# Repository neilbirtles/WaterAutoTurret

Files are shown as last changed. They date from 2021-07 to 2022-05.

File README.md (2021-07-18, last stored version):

# Water Auto Turret

This is a fully automatic water turret that will track people and fire water at them. Intended to be a toy for children in the summer! Its constructed from a mix of 3D printed parts, aluminium extrusions and various other off the shelf items. The unit is powered by a 12v lead acid battery and plugs into a standard hosepipe push on connector for its water supply. It uses a Khadas VIM3 board to control everything and uses the onboard NPU to do the object tracking.

Full design information will be published here for those that want to make one for themselves

Current stage of development is:
    Mechanics: 90% complete, all functional items are working, just a few covers and minor parts need to be constructed
    Electronics: 95% complete, there are a couple of errors that need to be fixed in the rev2 PCB, but otherwise working
    Software: 50% complete, drivers and test code complete for the water control solenoids and stepper motors and an interface to YOLOv3 is implemented along with initial web front end

## Mechanics

All mechanical items have been designed in Fusion360 - model files to be published. 3D printed items have been printed on a Prusa Mk3S+

## Electronics

Main controller board is a Khadas VIM3. A custom PCB is used to interface to the Water Auto Turret. The PCB mounts a DRV8806 chip for driving 4 solenoids for controlling water flow to the turret, two Trinamic TMC5160 breakout boards for controlling the pitch and yaw stepper motors and some battery monitoring / power control circuitry

## Software 

Interface between the control electronics and the Khadas VIM3 is via WiringPi and SPI dev coded in python so should allow for porting to other SBC such as Raspberry Pi, but there will be obvious limitations for the object tracking if a board without an NPU is used. 

TMC5160_driver.py       - provides a generic TMC5160 driver written in python using WiringPi and SPIdev 
motor_test.py           - exercises the TMC5160 driver and allows both motors to be homed and then manually and automatically moved 

DRV8806_driver.py       - provides a driver for the DRV8806 chip written in python using WiringPi
solenoids_test.py       - exercises the DRV8806 driver and does a simple sequence of closing and opening the 4 valves 

KhadasYolov3Detector    - uses the Khadas Yolo v3 demo from here https://gitlab.com/khadas/aml_npu_app and adds in a simple TCP server to output the detections in JSON format to allow them to be used by the main python application 

Webserver               - initial outline of a flask web front end to provide control info for the water auto turret

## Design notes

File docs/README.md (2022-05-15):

# Water Auto Turret
Welcome to the home of the Water Auto Turret! This project was borne out of the desire to use one of my excellent Khadas VIM3 SBC for something other than crypto currency mining and to provide an excellent (if I do say so myself!) toy for my daughter and her friends during the summer months. The motivation to finish it came from the [1st Khadas Community Competition](https://forum.khadas.com/t/khadas-1st-community-competition/14076) - thank you Khadas! I’ve used the VIM3 to create large crypto mining clusters so I knew they were high performance, well supported and well documented SBCs. One specific feature that I hadn’t used before was the Neural Processing Unit (NPU) and so this project was born to give a real world application to test this feature out. 

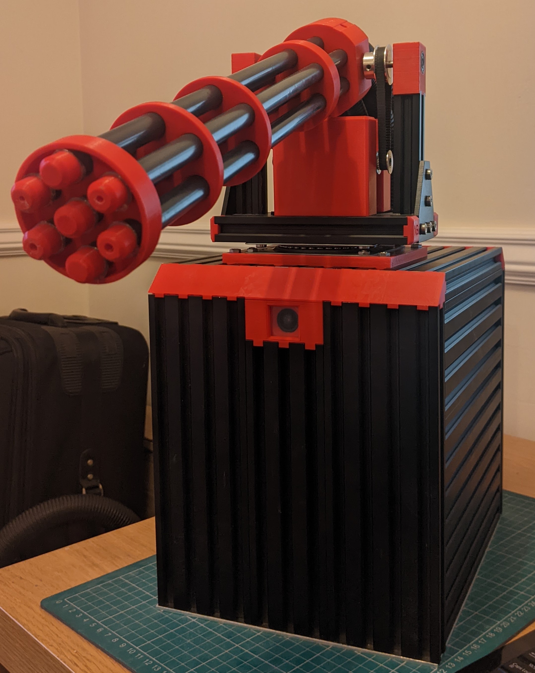
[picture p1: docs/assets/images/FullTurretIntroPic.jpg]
Water Auto Turret Overall Picture


The intention when designing and building this water turret was to minimise the custom design aspects and use off the shelf components (both hardware and software) as far as possible. This didn't always work out as there ended up being lots of custom 3D printed items, a custom PCB, custom extrusions and software however all of these aspects were made significantly easier due to the following companies I sourced parts and software from - I highly recommend them for any similar projects and work!:
* Khadas - OEM of the VIM3, fan, heatsink and the OS08A10 camera used in the project. They also provide excellent support for their products with full 3D CAD models available making the design of 3D printed parts that incorporate them a breeze, great documentation, great supporting software from operating systems to code to access the NPU (including via Python!) and a great forum with lots of community support - [Khadas](https://www.khadas.com/)
* Ooznest - source for all the aluminum extrusions, brackets and motors used in this project. Their fast, excellent and very accurate cut to size and tapping service for the extrusions made the core mechanical aspects of this project really easy to put together - [Ooznest](https://ooznest.co.uk/) 
* Prusa - source for my Prusa i3 MK3S+ 3D printer and the Prusament filament used to 3D print all parts in this project. The accuracy from this printer allowed repeatable production of friction fit parts making assembly of the Water Auto Turret significantly easier - [Prusa](https://www.prusa3d.com/) 
* Accu - source for all the fixings used in this project - this might not sound like the most exciting aspect but being able to easily and quickly (next day) get fixings of the lengths needed in stainless steel without massive minimum order quantities allowed rapid progress to be made without adding additional constraints / time into the design process. My order history on their site attests to their usefulness as ive bought everything from M1.4 screws to the M12 coach bolts used in making my daughters monkey bars (can be seen in the background of the demo video!) - [Accu](https://www.accu.co.uk/)

Heres a short video of the Water Auto Turret in action during its testing phase

<iframe width="560" height="315" src="https://www.youtube.com/embed/ZMWd3soy9fM" title="YouTube video player" frameborder="0" allow="accelerometer; autoplay; clipboard-write; encrypted-media; gyroscope; picture-in-picture" allowfullscreen></iframe>

The Water Auto Turret has been built from black anodised extrusions, Lipstick Red Prusament PLA for all 3D printed parts and stainless steel fixings because I like the combination of these colours but this is obviously left up to the individual to pick the colour scheme and combinations. The block diagram for the Water Auto Turret can be found below.

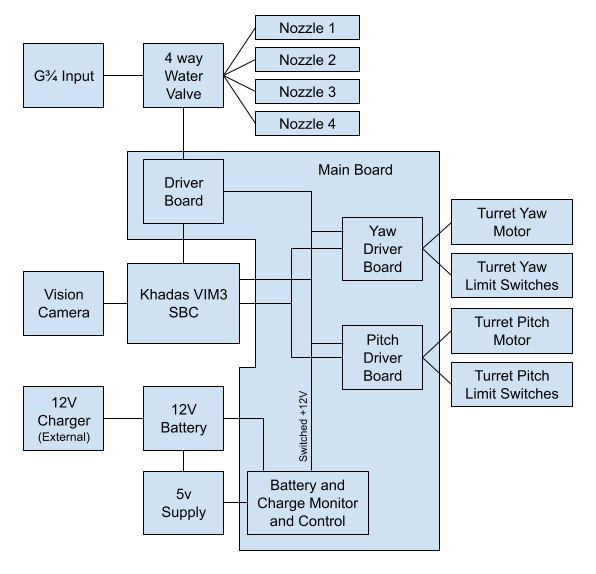
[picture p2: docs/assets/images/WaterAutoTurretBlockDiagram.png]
Block Diagram of the Water Auto Turret


### Controller
The heart of the system is the Khadas VIM3 SBC it provides the overall controller interfacing to a camera to provide the vision inputs, running the software for target identification and tracking (see the Software Description) and interfacing to a custom Main Board that provides:
* Control for pitch and yaw motors
* Control for water flow via solenoid valves 
* Power control with battery charging identification and voltage monitoring

The camera used in the system is a Khadas OS08A10 8MP HDR Camera. This plugs into the VIM3 via the MIPI-CSI port. The camera is housed in a custom 3D printed enclosure {02 Camera Enclosure} (the design of which was made way easier by the use of the Khadas provided CAD model of the camera!) that joins onto the main electronics enclosure that houses the VIM3 and Main Board.

### Main Board

The Main Board (see the [Controller PCB](https://github.com/neilbirtles/WaterAutoTurret/tree/main/Controller%20PCB)) for circuit diagrams, PCB layouts and firmware for the embedded microcontroller) for the system is designed as a daughter board for the VIM3 that plugs on via the 40 pin GPIO header and has fixing holes aligned to the VIM3 ones allowing both boards to be screwed together into the custom 3D printed electronics enclosure. Between the Main Board and VIM3 is a 3D printed heatsink cover to help direct airflow and a set of 3D printed spacers to keep the two boards correctly spaced when screwed in. A securing slot is also provided for the VIM3 wifi antenna to hold it in place in the enclosure. The {[00 Electronics Enclosure Base](https://github.com/neilbirtles/WaterAutoTurret/blob/main/3D%20Printable%20Parts/Electronics%20Enclosure/00%20Electronics%20Enclosure%20Base%20(Supports%20Needed).stl)} and {[01 Electronics Enclosure Lid](https://github.com/neilbirtles/WaterAutoTurret/blob/main/3D%20Printable%20Parts/Electronics%20Enclosure/01%20Electronics%20Enclosure%20Lid.stl)} have been designed to minimise the chances of water ingress whilst at the same time allowing all the required connections and airflow. All connections are via the bottom on the enclosure and are via grommets to minimise open areas. Air flow is via the front face of the enclosure with a plenum chamber (with water drain holes) to prevent direct water access. The air from this chamber is directed into the side of the VIM3 heatsink where it is pulled across the heatsink via the VIM3 heatsink fan. Exhaust air is pulled out of the enclosure via a fan in the bottom. A grommet strip is used to provide a seal between the lid and base and the interface to the camera housing has a lip preventing water entering via this direction as well. 

The Main Board provides control of the pitch and yaw motors for the Water Auto Turret Barrel through the use of TMC5160 motion controllers. These simplify overall system and software design by just allowing target positions to be sent to the controllers (post calibration) with the TMC5160 taking care of the complicated motor and position control. To further simplify the design [TMC5160 Breakout Boards](https://www.trinamic.com/support/eval-kits/details/tmc5160-bob/) have been used that incorporate the motor drive MOSFETs and all passives needed on a small form factor PCB that simply plugs into the Main Board via pin headers. These boards interface to the VIM3 via the SPI interface (GPIO pins 16 => CLK, 35 => SDO, 37 => SDI), with VIM3 GPIO pins used as chip select (CS) lines (GPIO pins 22 => Yaw Motor CS, 23 => Pitch Motor CS). The TMC5160 motion controller boards also incorporate lines for the use of limit switches. Two are used for each of the pitch and yaw motors to allow for homing. The motion controllers are capable of switch free homing but requires the motors to be running at reasonable speeds and to hit physical limits for sensing neither of which are present in this system.

### Water Control

Control of the water flow is provided via a standard 4 way normally closed solenoid valve. This valve has a standard G3/4 threaded input and 4 10mm outlets, each of which is individually controlled via a 12v solenoid. These solenoids are in turn controlled via a DRV8806 mounted on the Main Board that provides the required drivers for the solenoids and interfaces to the VIM3 via a simple clock and latch serial interface (GPIO pins 29 => SDI, 31 => SCLK, 32 => Latch, 33 => Reset (not used but wired in case useful). 4 of the 6 barrels on the overall Water Auto Turret barrel can therefore be used to squirt water at targets. Different size nozzles have been provided as 3D printed parts to allow for different ranges and volumes of water. These nozzle sizes can be configured for the water pressure present and the desired ranges. The number of nozzles used simultaneously can also affect the distance depending on the available water pressure. These nozzles are designed to slot inside the individual barrels and have been hot glued in place which provides a good balance between being able to change and a decent water seal. The solenoid valve has been chosen to be able to cope with mains water pressure and in the system I use has a standard push fit hosepipe fitting screwed onto the G3/4 thread to allow easy connection and disconnection from the water supply.

### Power

The entire system is powered via a 12v sealed lead acid battery. This provides a water safe way of providing the power required in a portable manner. No charging control circuit is contained in the system but a connector is provided to enable a standard 12v sealed lead acid battery charger to be connected to the system. A fan is provided (in a 3D printed housing to prevent water damage) to ensure ventilation of the Water Auto Turret base when the battery is charging. The Main Board monitors for this charging power input and also monitors the battery voltage to ensure that the battery is not over discharged. If either of these conditions are detected then the power to the VIM3, motor and solenoid controllers is removed and only restored once both these conditions are removed. This is achieved via a latching 12v relay to reduce power consumption. These control aspects are provided via a small PIC microcontroller that also provides indication (via LED on the power and water inlet 3D printed part) if either of these conditions are encountered. The firmware for this microcontroller can be found in the firmware subfolder of the PCB folder. The C source code is fully commented and is fairly simple so no explanation is provided here.

### Project Status

The Water Auto Turret is currently fully functional and capable of identifying, tracking and shooting targets (i.e. children!) with water. In work is an improvement to the frame rate of the tracking algorithm and improvement to accuracy of water shooting - especially in the more extreme left and right arcs of fire. 

### Build Guide

A complete description, build guide and bill of materials can be found in this repository so should be relatively straightforward for anyone that wants to replicate the project. Any questions then please just ask - I am more than willing to help.

Build Guide and Descriptions:
* [VIM3 Setup](VIM3Setup.md)
* [Software Description](SoftwareDescription.md)
* [3D Printed Parts](3DPrintedParts.md)
* [Mechanical Assembly](MechanicalAssembly.md)
* [Electronics Assembly](ElectronicsAssembly.md)
* [Full Bill of Maerials and Equipment Breakdown Strucutre](https://github.com/neilbirtles/WaterAutoTurret/tree/main/BoMandEBS.xlsx)

### 3D Models

A complete interactive 3D Model for the Water Auto Turret can be found [here](https://a360.co/3vnJYny) and an export of all the 3D components in both Fusion360 and step file formats can be found here [3D Models](https://github.com/neilbirtles/WaterAutoTurret/tree/main/Fusion360%20Files)

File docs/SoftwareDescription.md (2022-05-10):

# Software Description
The software for the Water Auto Turret has been implemented in four main parts:
* A Web Application using the Flask framework to provide the user interface
* The Khadas Software Neural Network (Python API) to carry out the computer vision to identify potential targets
* A turret controller that takes the potential targets and converts this to turret movement information and feeds this information back to the web front end
* Low level drivers to control the motors, solenoids etc.

The code has been pretty thoroughly commented so should be relatively self explanatory however and overview is given below. I am not a software developer and have self taught myself python so welcome any feedback on improvements and or better ways of implementing this code!

### Web Application
This is a standard Flask web application that is started using the command `python3 autoturret.py`

Within the [\_\_init__.py](https://github.com/neilbirtles/WaterAutoTurret/blob/main/Auto%20Turret%20Control%20Software/autoturretwebapp/__init__.py) file the following are initialised:
* motors - provides setup of the SPI / GPIO interfaces, initialisation (inc chip select pin definition) and carries out the homing for the  pitch_motor and yaw_motors. Both motors use the lower level TMC5160_driver for interfacing to the TMC5160 Breakout Boards.
* solenoids - provides setup and initialisation of the solenoid interface including the GPIO pins used for the interface to the lower level DRV8806 driver.
* detection_model_params - provides and initial setup of parameters for the detection model. Created to provide easier change in the future
* turret_controller - the turret controller which is where all the neural network processing is carried out. This is spawned in a separate thread to prevent the web app becoming blocked. Outputs from this thread are loaded into a standard Python Queue to allow the outputs to be grabbed by the web app to display on the front end.
* app_thread_pool - provides the thread pool (that the turret_controller is spawned in), events for notifications into/out of the thread and also the pipeline for exchanging information out of the thread

After this initialisation the Flask app is started and the system is ready for targets!

In the routes.py file the generate() function attempts to grabs video frames from the Queue and allows them to be displayed on the web front end. The rate this grab happens is adjusted to slightly faster than the current frame rate to get a decent refresh rate on the screen without this function looping instantly and using all processing power (as it did when I first wrote it…)

### KSNN Yolov3
The Water Auto Turret uses the Yolo v3 model to carry out the object detection and tracking. The code for this can be found in the [turret_controller.py](https://github.com/neilbirtles/WaterAutoTurret/blob/main/Auto%20Turret%20Control%20Software/autoturretwebapp/turret_controller.py) file and draws on the Khadas examples. The Yolo v3 model and lib files are the standard Khadas provided ones. 

The detection works as follows:
* Setup the KSNN
* Initialise the neural network with the Yolo v3 model
* Setup the opencv capture devices
* Loop around the following:
  * Grab a video frame
  * Carry out inference
  * Transform the returned data into the format required for post processing
  * Extract the bounding boxes, associated class names and probability scores from the returned data
  * Scale the grabbed frame to be the right size to display in the web front end
  * Get targets from the neural network returned data (including marking these up in the grabbed frame
  * Pass the grabbed frame into Queue to allow it to be grabbed by the web front end for display

### Turret Controller
The turret control software can also be found in the [turret_controller.py](https://github.com/neilbirtles/WaterAutoTurret/blob/main/Auto%20Turret%20Control%20Software/autoturretwebapp/turret_controller.py) file. The target detection loop through all the object detections passed out from the neural network processing and does the following checks on each to identify targets:
* Checks if the detected object is a “person” and if the probability is above the detection threshold
* If both are true then annotate the target in the image frame with “TARGET ACQUIRED”
* Calculate the mid point of the target to allow the Water Auto Turret to target it with water
* Draw a red * at the midpoint of the target in the image frame
* Scale the target image coordinates into the pitch and yaw step ranges (calculated during the initial homing procedure)
* Check if the difference in the new target coordinate is greater than the move threshold in both pitch and yaw motions
* If the difference is greater than the move threshold then move the appropriate motor(s) to the new target positions
* If there are one or more targets then turn on the water and if there arent then turn off the water (at the current time all 4 water ports are turned on or off at the same time)

### Low Level Drivers
#### TMC5160
The driver for this is provided in [TMC5160_driver.py](https://github.com/neilbirtles/WaterAutoTurret/blob/main/Auto%20Turret%20Control%20Software/autoturretwebapp/TMC5160_driver.py). The driver exposes all the functions of the TMC5160 that are currently used and have been used in development but does not provide all features of the TMC5160 device. The internal __read_from_TMC_5160 and __write_to_TMC5160 functions provide the interface direct to the chip. Other higher level functions are exposed from the driver such as “home”. The code in this file is well documented and is directly derived from the [TMC5160 datasheet](https://www.trinamic.com/fileadmin/assets/Products/ICs_Documents/TMC5160A_datasheet_rev1.16.pdf) so should be read in conjunction with the datasheet to get a full understanding of how it works.

#### DRV8806
The driver for this is provided in the [DRV8806_driver.py](https://github.com/neilbirtles/WaterAutoTurret/blob/main/Auto%20Turret%20Control%20Software/autoturretwebapp/DRV8806_driver.py). This should again be read in conjunction with the datasheet for the [DRV8806](https://www.ti.com/lit/gpn/drv8806) but this is much simpler than the TMC5160 as the interface is essentially - set or reset the data bit to indicate a solenoid driving being on or off respectively, clock this data bit into the device by strobing the clock line, repeat this 3 times more to get data bits for all 4 outputs into the device and then latch that data into the outputs. Again the code is documented so should be easy to understand. 

### Tests
In the “Tests” folder there are some standalone test files that can be used when debugging the system or for testing during assembly
* [motor_test.py](https://github.com/neilbirtles/WaterAutoTurret/blob/main/Auto%20Turret%20Control%20Software/Tests/motor_test.py) - allows for manual homing and setup whilst providing low level feedback from the driver code. The functionality for this can be seen from the code or from running the file and reading the prompts
* [solenoids_test.py](https://github.com/neilbirtles/WaterAutoTurret/blob/main/Auto%20Turret%20Control%20Software/Tests/solenoids_test.py) - provides a sequence that turns on each solenoid valve in sequence 0.5 seconds apart, waits 1 second and then turns them off in sequence 0.5 seconds apart. This produces an audible clicking that can be used to ensure all solenoids are working

## Future Software Development
The Water Auto Turret is currently fully functional, however its always possible to get better! For this reason the following areas of software are currently under development:
* Improved target tracking using OpenCV for detection at a reduced frame rate and then using the much lighter weight [Dlib for tracking](http://dlib.net/correlation_tracker.py.html) with the aim or providing more frequent updates to the targeting 
* Improved alignment between objects being tracked and targeting - at the moment this is a linear scale relationship and this doesn't work as well as it could as the target moves away from centre

[{Home}](README.md) [{Next}](3DPrintedParts.md)

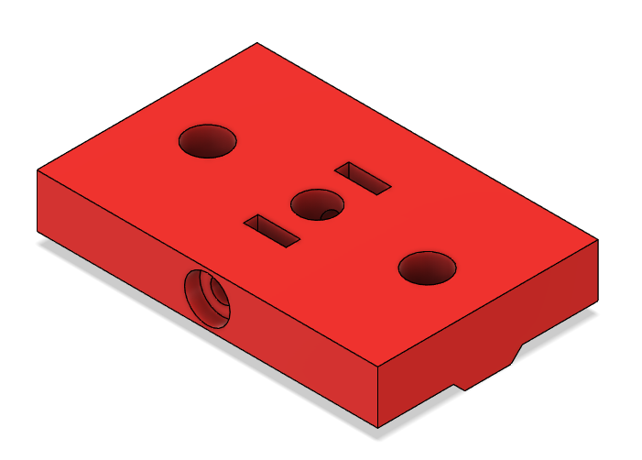
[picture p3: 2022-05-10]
docs/assets/images/BarrelMountRotaryAttachment.PNG

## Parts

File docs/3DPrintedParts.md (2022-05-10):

# 3D Printed Parts

All 3D printed parts were printed from PLA on a Prusa Mk3s, using standard settings. Only those parts that have their names appended with “(Supports Needed)” need supports enabled, all other parts have been designed specifically to be printed support free. All parts have been saved in the correct orientation for printing to simplify the process. As they can be added to your slicer of choice, sliced and printed. The variable layer height feature was used on all the parts to speed up the print time as there are quite a lot of parts to be printed!

On a well setup printer the parts will be of the correct size to fit together, with many of the parts being friction fit into the aluminum profiles and over the plastic tubing the barrel is constructed from. It is however usually worth pushing the parts designed to slot into the aluminum profiles through a spare piece of profile to make sure they are a tight but not unreasonable fit. Where the fit is too tight sliding them in and out of a aluminum profile a few times (with the help of a rubber mallet if needed!) will get them to the perfect fit.

File names for the stl files link back to body names in the Fusion360 model for the water turret so allow for easy identification. The following are the parts that need supports along with a suggested description of where the supports are needed. The Prusa Slicer support painter feature was used to limit the supports to where they were needed to avoid large amounts of unneeded support material that would need to be removed.

* Electronics Enclosure::[00 Electronics Enclosure Base (Supports Needed).stl](https://github.com/neilbirtles/WaterAutoTurret/blob/main/3D%20Printable%20Parts/Electronics%20Enclosure/00%20Electronics%20Enclosure%20Base%20(Supports%20Needed).stl) - supports only needed along the very top side (when orienting the part as saved, and the side that joins to the camera housing), all other areas can be masked off or have maximum 45 degree angles to allow supportless printing

* Turret Barrel Mount::[04 Barrel Microswitch Mount - Front (Supports Needed).stl](https://github.com/neilbirtles/WaterAutoTurret/blob/main/3D%20Printable%20Parts/Turret%20Barrel%20Mount/04%20Barrel%20Microswitch%20Mount%20-%20Front%20(Supports%20N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) - supports needed for at least the circular locator pins that hold the microswitch in place and the top edge. Usually just let the slicer add supports wherever it like for these parts. Just need to be careful when removing them to avoid breaking the locator pins. 

* Turret Barrel Mount::[05 Barrel Microswitch Mount - Rear (Supports Needed).stl](https://github.com/neilbirtles/WaterAutoTurret/blob/main/3D%20Printable%20Parts/Turret%20Barrel%20Mount/05%20Barrel%20Microswitch%20Mount%20-%20Rear%20(Supports%20Ne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) - as front microswitch mount above.

* Turret Base::[02 Internal Limit Switch Holder - Left (Supports Needed).stl](https://github.com/neilbirtles/WaterAutoTurret/blob/main/3D%20Printable%20Parts/Turret%20Base/02%20Internal%20Limit%20Switch%20Holder%20-%20Left%20(Supports%20Needed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) - as front microswitch mount above.

* Turret Base::[03 Internal Limit Switch Holder - Right (Supports Needed).stl](https://github.com/neilbirtles/WaterAutoTurret/blob/main/3D%20Printable%20Parts/Turret%20Base/03%20Internal%20Limit%20Switch%20Holder%20-%20Right%20(Supports%20Neede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) - as front microswitch mount above.

* Turret Base::[09 Water and Power Inlet (Supports Needed).stl](https://github.com/neilbirtles/WaterAutoTurret/blob/main/3D%20Printable%20Parts/Turret%20Base/09%20Water%20and%20Power%20Inlet%20(Supports%20Needed).stl) - can either pick supports to build plate only or paint on supports down the both sides to support the parts that slot into the aluminum profiles. 

The use of all the 3D printed parts can be found in the rest of the build guide and also in the Fusion360 model. All the 3D printed parts are stored [here](https://github.com/neilbirtles/WaterAutoTurret/tree/main/3D%20Printable%20Parts)

[{Home}](README.md) [{Next}](MechanicalAssembly.md)

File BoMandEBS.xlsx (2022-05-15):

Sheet: EBS
Level |  |  |  |  |  |  | Source | Price
0 | Water Auto Turret
1 |  | Turret Base
2 |  |  | Internal Bearing and Motor Mount
3 |  |  |  | 00 Bearing Mount |  | 00 Bearing Mount | https://github.com/neilbirtles/WaterAutoTurret/blob/main/3D%20Printable%20Parts/Internal%20Bearing%20and%20Motor%20Mount/00%20Bearing%20Mount.stl
3 |  |  |  | M3 square nut |  | M3 square nut
3 |  |  |  | M3 square nut |  | M3 square nut
3 |  |  |  | M3x25mm Cap head screw |  | M3x25mm Cap head screw
3 |  |  |  | M3x25mm Cap head screw |  | M3x25mm Cap head screw
3 |  |  |  | 625ZZ bearing |  | 625ZZ bearing
3 |  |  |  | 625ZZ bearing |  | 625ZZ bearing
3 |  |  |  | 20x40x150mm aluminum extrusion, black annodise, untapped |  | 20x40x150mm aluminum extrusion, black annodise, untapped
3 |  |  |  | 01 Battery Top Spacer |  | 01 Battery Top Spacer | https://github.com/neilbirtles/WaterAutoTurret/blob/main/3D%20Printable%20Parts/Internal%20Bearing%20and%20Motor%20Mount/01%20Battery%20Top%20Spacer.stl
3 |  |  |  | 70x40x2mm foam rectangle |  | 70x40x2mm foam rectangle
3 |  |  |  | M5 tee nut |  | M5 tee nut
3 |  |  |  | M5 tee nut |  | M5 tee nut
3 |  |  |  | M5 tee nut |  | M5 tee nut
3 |  |  |  | M5 tee nut |  | M5 tee nut
3 |  |  |  | NEMA17 Motor Bracket |  | NEMA17 Motor Bracket
3 |  |  |  | M5x8mm Cap head screw |  | M5x8mm Cap head screw
3 |  |  |  | M5x8mm Cap head screw |  | M5x8mm Cap head screw
3 |  |  |  | M5x8mm Cap head screw |  | M5x8mm Cap head screw
3 |  |  |  | M5x8mm Cap head screw |  | M5x8mm Cap head screw
3 |  |  |  | M3x6mm Cap head screw |  | M3x6mm Cap head screw
3 |  |  |  | M3x6mm Cap head screw |  | M3x6mm Cap head screw
3 |  |  |  | M3x6mm Cap head screw |  | M3x6mm Cap head screw
3 |  |  |  | M3x6mm Cap head screw |  | M3x6mm Cap head screw
3 |  |  |  | NEMA17 Motor |  | NEMA17 Motor
3 |  |  |  | 16 Tooth, 5mm bore, 2GT Pulley |  | 16 Tooth, 5mm bore, 2GT Pulley
3 |  |  |  | M5 tee nut |  | M5 tee nut
3 |  |  |  | M5 tee nut |  | M5 tee nut
3 |  |  |  | M5 tee nut |  | M5 tee nut
3 |  |  |  | M5 tee nut |  | M5 tee nut
3 |  |  |  | M5 tee nut |  | M5 tee nut
3 |  |  |  | M5 tee nut |  | M5 tee nut
3 |  |  |  | L bracket - double, black annodise |  | L bracket - double, black annodise
3 |  |  |  | L bracket - double, black annodise |  | L bracket - double, black annodise
3 |  |  |  | M5x8mm Cap head screw |  | M5x8mm Cap head screw
3 |  |  |  | M5x8mm Cap head screw |  | M5x8mm Cap head screw
3 |  |  |  | M5x8mm Cap head screw |  | M5x8mm Cap head screw
3 |  |  |  | M5x8mm Cap head screw |  | M5x8mm Cap head screw
2 |  |  | Water and Power Inlet
3 |  |  |  | 09 Water and Power Inlet {3D Printed} |  | 09 Water and Power Inlet {3D Printed}
3 |  |  |  | IP68 DC Power Socket |  | IP68 DC Power Socket | https://uk.rs-online.com/web/p/dc-power-connectors/7051525
3 |  |  |  | DC Power Socket Cover |  | DC Power Socket Cover | https://uk.rs-online.com/web/p/av-connector-accessories/7249019
3 |  |  |  | 5mm bi-colour red/green LED |  | 5mm bi-colour red/green LED | https://uk.rs-online.com/web/p/leds/2285770
3 |  |  |  | SPST Toggle Switch, Latching, IP67, Panel Mount |  | SPST Toggle Switch, Latching, IP67, Panel Mount | https://uk.rs-online.com/web/p/toggle-switches/1813642
3 |  |  |  | Switch sealing hood |  | Switch sealing hood | https://uk.rs-online.com/web/p/toggle-switch-sealing-hoods/1253525
3 |  |  |  | 12v Electric Solenoid Valve,Solenoid Valve,G3/4" 1 in 4 out |  | 12v Electric Solenoid Valve,Solenoid Valve,G3/4" 1 in 4 out | https://www.amazon.co.uk/gp/product/B07TYCQ4JN
3 |  |  |  | M4x16mm Cap Head screw |  | M4x16mm Cap Head screw
3 |  |  |  | G3/4" to quick connect adaptor |  | G3/4" to quick connect adaptor | https://www.amazon.co.uk/gp/product/B07NP9Q25F
3 |  |  |  | Quick disconnect crimp terminal |  | Quick disconnect crimp terminal | https://uk.farnell.com/amp-te-connectivity/640903-1/crimp-terminal-female-red/dp/586833
3 |  |  |  | Quick disconnect crimp terminal |  | Quick disconnect crimp terminal | https://uk.farnell.com/amp-te-connectivity/640903-1/crimp-terminal-female-red/dp/586833
3 |  |  |  | Quick disconnect crimp terminal |  | Quick disconnect crimp terminal | https://uk.farnell.com/amp-te-connectivity/640903-1/crimp-terminal-female-red/dp/586833
3 |  |  |  | Quick disconnect crimp terminal |  | Quick disconnect crimp terminal | https://uk.farnell.com/amp-te-connectivity/640903-1/crimp-terminal-female-red/dp/586833
3 |  |  |  | Quick disconnect crimp terminal |  | Quick disconnect crimp terminal | https://uk.farnell.com/amp-te-connectivity/640903-1/crimp-terminal-female-red/dp/586833
3 |  |  |  | Quick disconnect crimp terminal |  | Quick disconnect crimp terminal | https://uk.farnell.com/amp-te-connectivity/640903-1/crimp-terminal-female-red/dp/586833
3 |  |  |  | Quick disconnect crimp terminal |  | Quick disconnect crimp terminal | https://uk.farnell.com/amp-te-connectivity/640903-1/crimp-terminal-female-red/dp/586833
3 |  |  |  | Quick disconnect crimp terminal |  | Quick disconnect crimp terminal | https://uk.farnell.com/amp-te-connectivity/640903-1/crimp-terminal-female-red/dp/586833
2 |  |  | Fan Inlet
3 |  |  |  | 00 Fan Inlet {3D Printed} |  | 00 Fan Inlet {3D Printed}
3 |  |  |  | 40x40x10mm 12v DC Fan |  | 40x40x10mm 12v DC Fan | https://www.amazon.co.uk/gp/product/B07CM1PQNS
3 |  |  |  | M4x20mm Cap head screw |  | M4x20mm Cap head screw
3 |  |  |  | M4x20mm Cap head screw |  | M4x20mm Cap head screw
3 |  |  |  | M4x20mm Cap head screw |  | M4x20mm Cap head screw
3 |  |  |  | M4x20mm Cap head screw |  | M4x20mm Cap head screw
3 |  |  |  | M4 Hex Nut |  | M4 Hex Nut
3 |  |  |  | M4 Hex Nut |  | M4 Hex Nut
3 |  |  |  | M4 Hex Nut |  | M4 Hex Nut
3 |  |  |  | M4 Hex Nut |  | M4 Hex Nut
3 |  |  |  | 01 Fan Inlet Hole Cover {3D Printed} |  | 01 Fan Inlet Hole Cover {3D Printed}
3 |  |  |  | 01 Fan Inlet Hole Cover {3D Printed} |  | 01 Fan Inlet Hole Cover {3D Printed}
3 |  |  |  | 01 Fan Inlet Hole Cover {3D Printed} |  | 01 Fan Inlet Hole Cover {3D Printed}
3 |  |  |  | 01 Fan Inlet Hole Cover {3D Printed} |  | 01 Fan Inlet Hole Cover {3D Printed}
2 |  |  | Rotary Bearing Mount
3 |  |  |  | 04 Rotary Bearing Mount {3D Printed} |  | 04 Rotary Bearing Mount {3D Printed}
3 |  |  |  | M5x12mm hex head screw |  | M5x12mm hex head screw
3 |  |  |  | M5x12mm hex head screw |  | M5x12mm hex head screw
3 |  |  |  | M5x12mm hex head screw |  | M5x12mm hex head screw
3 |  |  |  | M5x12mm hex head screw |  | M5x12mm hex head screw
3 |  |  |  | M5 Thin hex nut |  | M5 Thin hex nut | https://www.accu.co.uk/thin-hexagon-nuts/73060-HFN-M5-A2
3 |  |  |  | M5 Thin hex nut |  | M5 Thin hex nut | https://www.accu.co.uk/thin-hexagon-nuts/73060-HFN-M5-A2
3 |  |  |  | M5 Thin hex nut |  | M5 Thin hex nut | https://www.accu.co.uk/thin-hexagon-nuts/73060-HFN-M5-A2
3 |  |  |  | M5 Thin hex nut |  | M5 Thin hex nut | https://www.accu.co.uk/thin-hexagon-nuts/73060-HFN-M5-A2
2 |  |  | Turret Base Top Plate and Plumbing
3 |  |  |  | 45mm length 10mm ID braided hose |  | 45mm length 10mm ID braided hose | https://www.amazon.co.uk/gp/product/B076BNY9PF
3 |  |  |  | 45mm length 10mm ID braided hose |  | 45mm length 10mm ID braided hose | https://www.amazon.co.uk/gp/product/B076BNY9PF
3 |  |  |  | 90 degree 10mm hose connector |  | 90 degree 10mm hose connector | https://www.amazon.co.uk/gp/product/B008YGFQV0
3 |  |  |  | 07 Tubing Adaptor {3D Printed} |  | 07 Tubing Adaptor {3D Printed}
3 |  |  |  | Hose clip 11-16mm |  | Hose clip 11-16mm | https://uk.rs-online.com/web/p/hose-clips-jubilee-clips/0525183
3 |  |  |  | Hose clip 11-16mm |  | Hose clip 11-16mm | https://uk.rs-online.com/web/p/hose-clips-jubilee-clips/0525183
3 |  |  |  | Hose clip 11-16mm |  | Hose clip 11-16mm | https://uk.rs-online.com/web/p/hose-clips-jubilee-clips/0525183
3 |  |  |  | 45mm length 10mm ID braided hose |  | 45mm length 10mm ID braided hose | https://www.amazon.co.uk/gp/product/B076BNY9PF
3 |  |  |  | 45mm length 10mm ID braided hose |  | 45mm length 10mm ID braided hose | https://www.amazon.co.uk/gp/product/B076BNY9PF
3 |  |  |  | 90 degree 10mm hose connector |  | 90 degree 10mm hose connector | https://www.amazon.co.uk/gp/product/B008YGFQV0
3 |  |  |  | 07 Tubing Adaptor {3D Printed} |  | 07 Tubing Adaptor {3D Printed}
3 |  |  |  | Hose clip 11-16mm |  | Hose clip 11-16mm | https://uk.rs-online.com/web/p/hose-clips-jubilee-clips/0525183
3 |  |  |  | Hose clip 11-16mm |  | Hose clip 11-16mm | https://uk.rs-online.com/web/p/hose-clips-jubilee-clips/0525183
3 |  |  |  | Hose clip 11-16mm |  | Hose clip 11-16mm | https://uk.rs-online.com/web/p/hose-clips-jubilee-clips/0525183
3 |  |  |  | 130mm length 10mm ID braided hose |  | 130mm length 10mm ID braided hose | https://www.amazon.co.uk/gp/product/B076BNY9PF
3 |  |  |  | 65mm length 10mm ID braided hose |  | 65mm length 10mm ID braided hose | https://www.amazon.co.uk/gp/product/B076BNY9PF
3 |  |  |  | 45mm length 10mm ID braided hose |  | 45mm length 10mm ID braided hose | https://www.amazon.co.uk/gp/product/B076BNY9PF
3 |  |  |  | 90 degree 10mm hose connector |  | 90 degree 10mm hose connector | https://www.amazon.co.uk/gp/product/B008YGFQV0
3 |  |  |  | 90 degree 10mm hose connector |  | 90 degree 10mm hose connector | https://www.amazon.co.uk/gp/product/B008YGFQV0
3 |  |  |  | 07 Tubing Adaptor {3D Printed} |  | 07 Tubing Adaptor {3D Printed}
3 |  |  |  | Hose clip 11-16mm |  | Hose clip 11-16mm | https://uk.rs-online.com/web/p/hose-clips-jubilee-clips/0525183
3 |  |  |  | Hose clip 11-16mm |  | Hose clip 11-16mm | https://uk.rs-online.com/web/p/hose-clips-jubilee-clips/0525183
3 |  |  |  | Hose clip 11-16mm |  | Hose clip 11-16mm | https://uk.rs-online.com/web/p/hose-clips-jubilee-clips/0525183
3 |  |  |  | Hose clip 11-16mm |  | Hose clip 11-16mm | https://uk.rs-online.com/web/p/hose-clips-jubilee-clips/0525183
3 |  |  |  | Hose clip 11-16mm |  | Hose clip 11-16mm | https://uk.rs-online.com/web/p/hose-clips-jubilee-clips/0525183
3 |  |  |  | 130mm length 10mm ID braided hose |  | 130mm length 10mm ID braided hose | https://www.amazon.co.uk/gp/product/B076BNY9PF
3 |  |  |  | 65mm length 10mm ID braided hose |  | 65mm length 10mm ID braided hose | https://www.amazon.co.uk/gp/product/B076BNY9PF
3 |  |  |  | 45mm length 10mm ID braided hose |  | 45mm length 10mm ID braided hose | https://www.amazon.co.uk/gp/product/B076BNY9PF
3 |  |  |  | 90 degree 10mm hose connector |  | 90 degree 10mm hose connector | https://www.amazon.co.uk/gp/product/B008YGFQV0
3 |  |  |  | 90 degree 10mm hose connector |  | 90 degree 10mm hose connector | https://www.amazon.co.uk/gp/product/B008YGFQV0
3 |  |  |  | 07 Tubing Adaptor {3D Printed} |  | 07 Tubing Adaptor {3D Printed}
3 |  |  |  | Hose clip 11-16mm |  | Hose clip 11-16mm | https://uk.rs-online.com/web/p/hose-clips-jubilee-clips/0525183
3 |  |  |  | Hose clip 11-16mm |  | Hose clip 11-16mm | https://uk.rs-online.com/web/p/hose-clips-jubilee-clips/0525183
3 |  |  |  | Hose clip 11-16mm |  | Hose clip 11-16mm | https://uk.rs-online.com/web/p/hose-clips-jubilee-clips/0525183
3 |  |  |  | Hose clip 11-16mm |  | Hose clip 11-16mm | https://uk.rs-online.com/web/p/hose-clips-jubilee-clips/0525183
3 |  |  |  | Hose clip 11-16mm |  | Hose clip 11-16mm | https://uk.rs-online.com/web/p/hose-clips-jubilee-clips/0525183
3 |  |  |  | 320mm 12mm ID, 15.8mm OD corrugated hose |  | 320mm 12mm ID, 15.8mm OD corrugated hose | https://www.amazon.co.uk/gp/product/B08JPMYB8B
3 |  |  |  | 08 Turret Base Top Plate {3D Printed} |  | 08 Turret Base Top Plate {3D Printed} | https://github.com/neilbirtles/WaterAutoTurret/blob/main/3D%20Printable%20Parts/Turret%20Base/08%20Turret%20Base%20Top%20Plate.stl
2 |  |  | Extrusion 20x80, black anodise, 240mm, no tap |  |  | Extrusion 20x80, black anodise, 240mm, no tap
2 |  |  | Extrusion 20x80, black anodise, 240mm, no tap |  |  | Extrusion 20x80, black anodise, 240mm, no tap
2 |  |  | Extrusion 20x80, black anodise, 240mm, no tap |  |  | Extrusion 20x80, black anodise, 240mm, no tap
2 |  |  | 11 Profile Joiner {3D Printed} |  |  | 11 Profile Joiner {3D Printed}
2 |  |  | 11 Profile Joiner {3D Printed} |  |  | 11 Profile Joiner {3D Printed}
2 |  |  | 11 Profile Joiner {3D Printed} |  |  | 11 Profile Joiner {3D Printed}
2 |  |  | 11 Profile Joiner {3D Printed} |  |  | 11 Profile Joiner {3D Printed}
2 |  |  | Extrusion 20x80, black anodise, 240mm, no tap |  |  | Extrusion 20x80, black anodise, 240mm, no tap
2 |  |  | Extrusion 20x80, black anodise, 240mm, no tap |  |  | Extrusion 20x80, black anodise, 240mm, no tap
2 |  |  | Extrusion 20x80, black anodise, 240mm, no tap |  |  | Extrusion 20x80, black anodise, 240mm, no tap
2 |  |  | 11 Profile Joiner {3D Printed} |  |  | 11 Profile Joiner {3D Printed}
2 |  |  | 11 Profile Joiner {3D Printed} |  |  | 11 Profile Joiner {3D Printed}
2 |  |  | 11 Profile Joiner {3D Printed} |  |  | 11 Profile Joiner {3D Printed}
2 |  |  | 11 Profile Joiner {3D Printed} |  |  | 11 Profile Joiner {3D Printed}
2 |  |  | Extrusion 20x80, black anodise, 240mm, one end tapped |  |  | Extrusion 20x80, black anodise, 240mm, one end tapped
2 |  |  | Extrusion 20x60, black anodise, 90mm, no tap |  |  | Extrusion 20x60, black anodise, 90mm, no tap
2 |  |  | 11 Profile Joiner {3D Printed} |  |  | 11 Profile Joiner {3D Printed}
2 |  |  | 11 Profile Joiner {3D Printed} |  |  | 11 Profile Joiner {3D Printed}
2 |  |  | Extrusion 20x60, black anodise, 40mm, one end tapped |  |  | Extrusion 20x60, black anodise, 40mm, one end tapped
2 |  |  | 11 Profile Joiner {3D Printed} |  |  | 11 Profile Joiner {3D Printed}
2 |  |  | 11 Profile Joiner {3D Printed} |  |  | 11 Profile Joiner {3D Printed}
2 |  |  | Extrusion 20x80, black anodise, 240mm, one end tapped |  |  | Extrusion 20x80, black anodise, 240mm, one end tapped
2 |  |  | 11 Profile Joiner {3D Printed} |  |  | 11 Profile Joiner {3D Printed}
2 |  |  | 11 Profile Joiner {3D Printed} |  |  | 11 Profile Joiner {3D Printed}
2 |  |  | 11 Profile Joiner {3D Printed} |  |  | 11 Profile Joiner {3D Printed}
2 |  |  | 11 Profile Joiner {3D Printed} |  |  | 11 Profile Joiner {3D Printed}
2 |  |  | Extrusion 20x80, black anodise, 240mm, no tap |  |  | Extrusion 20x80, black anodise, 240mm, no tap
2 |  |  | 11 Profile Joiner {3D Printed} |  |  | 11 Profile Joiner {3D Printed}
2 |  |  | 11 Profile Joiner {3D Printed} |  |  | 11 Profile Joiner {3D Printed}
2 |  |  | Extrusion 20x60, black anodise, 50mm, no tap |  |  | Extrusion 20x60, black anodise, 50mm, no tap
2 |  |  | Extrusion 20x80, black anodise, 240mm, no tap |  |  | Extrusion 20x80, black anodise, 240mm, no tap
2 |  |  | 11 Profile Joiner {3D Printed} |  |  | 11 Profile Joiner {3D Printed}
2 |  |  | 11 Profile Joiner {3D Printed} |  |  | 11 Profile Joiner {3D Printed}
2 |  |  | Double universal L brackets |  |  | Double universal L brackets
2 |  |  | Double universal L brackets |  |  | Double universal L brackets
2 |  |  | Double universal L brackets |  |  | Double universal L brackets
2 |  |  | Double universal L brackets |  |  | Double universal L brackets
2 |  |  | Double universal L brackets |  |  | Double universal L brackets
2 |  |  | Double universal L brackets |  |  | Double universal L brackets
2 |  |  | Double universal L brackets |  |  | Double universal L brackets
2 |  |  | M5 tee nut |  |  | M5 tee nut
2 |  |  | M5 tee nut |  |  | M5 tee nut
2 |  |  | M5 tee nut |  |  | M5 tee nut
2 |  |  | M5 tee nut |  |  | M5 tee nut
2 |  |  | M5 tee nut |  |  | M5 tee nut
2 |  |  | M5 tee nut |  |  | M5 tee nut
2 |  |  | M5 tee nut |  |  | M5 tee nut
2 |  |  | M5 tee nut |  |  | M5 tee nut
2 |  |  | M5 tee nut |  |  | M5 tee nut
2 |  |  | M5 tee nut |  |  | M5 tee nut
2 |  |  | M5 tee nut |  |  | M5 tee nut
2 |  |  | M5 tee nut |  |  | M5 tee nut
2 |  |  | M5 tee nut |  |  | M5 tee nut
2 |  |  | M5 tee nut |  |  | M5 tee nut
2 |  |  | M5 tee nut |  |  | M5 tee nut
2 |  |  | M5 tee nut |  |  | M5 tee nut
2 |  |  | M5 tee nut |  |  | M5 tee nut
2 |  |  | M5 tee nut |  |  | M5 tee nut
2 |  |  | M5 tee nut |  |  | M5 tee nut
2 |  |  | M5 tee nut |  |  | M5 tee nut
2 |  |  | M5 tee nut |  |  | M5 tee nut
2 |  |  | M5 tee nut |  |  | M5 tee nut
2 |  |  | M5 tee nut |  |  | M5 tee nut
2 |  |  | M5 tee nut |  |  | M5 tee nut
2 |  |  | M5 tee nut |  |  | M5 tee nut
2 |  |  | M5 tee nut |  |  | M5 tee nut
2 |  |  | M5x8mm Cap head screw |  |  | M5x8mm Cap head screw
2 |  |  | M5x8mm Cap head screw |  |  | M5x8mm Cap head screw
2 |  |  | M5x8mm Cap head screw |  |  | M5x8mm Cap head screw
2 |  |  | M5x8mm Cap head screw |  |  | M5x8mm Cap head screw
2 |  |  | M5x8mm Cap head screw |  |  | M5x8mm Cap head screw
2 |  |  | M5x8mm Cap head screw |  |  | M5x8mm Cap head screw
2 |  |  | M5x8mm Cap head screw |  |  | M5x8mm Cap head screw
2 |  |  | M5x8mm Cap head screw |  |  | M5x8mm Cap head screw
2 |  |  | M5x8mm Cap head screw |  |  | M5x8mm Cap head screw
2 |  |  | M5x8mm Cap head screw |  |  | M5x8mm Cap head screw
2 |  |  | M5x8mm Cap head screw |  |  | M5x8mm Cap head screw
2 |  |  | M5x8mm Cap head screw |  |  | M5x8mm Cap head screw
2 |  |  | M5x8mm Cap head screw |  |  | M5x8mm Cap head screw
2 |  |  | M5x8mm Cap head screw |  |  | M5x8mm Cap head screw
2 |  |  | M5x8mm Cap head screw |  |  | M5x8mm Cap head screw
2 |  |  | M5x8mm Cap head screw |  |  | M5x8mm Cap head screw
2 |  |  | M5x8mm Cap head screw |  |  | M5x8mm Cap head screw
2 |  |  | M5x8mm Cap head screw |  |  | M5x8mm Cap head screw
2 |  |  | M5x8mm Cap head screw |  |  | M5x8mm Cap head screw
2 |  |  | M5x8mm Cap head screw |  |  | M5x8mm Cap head screw
2 |  |  | M5x8mm Cap head screw |  |  | M5x8mm Cap head screw
2 |  |  | M5x8mm Cap head screw |  |  | M5x8mm Cap head screw
2 |  |  | M5x8mm Cap head screw |  |  | M5x8mm Cap head screw
2 |  |  | M5x8mm Cap head screw |  |  | M5x8mm Cap head screw
2 |  |  | M5x8mm Cap head screw |  |  | M5x8mm Cap head screw
2 |  |  | M5x8mm Cap head screw |  |  | M5x8mm Cap head screw
2 |  |  | 05 Top Rear Edge {3D Printed} |  |  | 05 Top Rear Edge {3D Printed}
2 |  |  | Double universal L brackets |  |  | Double universal L brackets
2 |  |  | Double universal L brackets |  |  | Double universal L brackets
2 |  |  | M5 tee nut |  |  | M5 tee nut
2 |  |  | M5 tee nut |  |  | M5 tee nut
2 |  |  | M5 tee nut |  |  | M5 tee nut
2 |  |  | M5 tee nut |  |  | M5 tee nut
2 |  |  | M5 tee nut |  |  | M5 tee nut
2 |  |  | M5 tee nut |  |  | M5 tee nut
2 |  |  | M5 tee nut |  |  | M5 tee nut
2 |  |  | M5 tee nut |  |  | M5 tee nut
2 |  |  | M5x8mm Cap head screw |  |  | M5x8mm Cap head screw
2 |  |  | M5x8mm Cap head screw |  |  | M5x8mm Cap head screw
2 |  |  | M5x8mm Cap head screw |  |  | M5x8mm Cap head screw
2 |  |  | M5x8mm Cap head screw |  |  | M5x8mm Cap head screw
2 |  |  | M5x8mm Cap head screw |  |  | M5x8mm Cap head screw
2 |  |  | M5x8mm Cap head screw |  |  | M5x8mm Cap head screw
2 |  |  | M5x8mm Cap head screw |  |  | M5x8mm Cap head screw
2 |  |  | M5x8mm Cap head screw |  |  | M5x8mm Cap head screw
2 |  |  | Hose clip 11-16mm |  |  | Hose clip 11-16mm | https://uk.rs-online.com/web/p/hose-clips-jubilee-clips/0525183
2 |  |  | Hose clip 11-16mm |  |  | Hose clip 11-16mm | https://uk.rs-online.com/web/p/hose-clips-jubilee-clips/0525183
2 |  |  | Hose clip 11-16mm |  |  | Hose clip 11-16mm | https://uk.rs-online.com/web/p/hose-clips-jubilee-clips/0525183
2 |  |  | Hose clip 11-16mm |  |  | Hose clip 11-16mm | https://uk.rs-online.com/web/p/hose-clips-jubilee-clips/0525183
2 |  |  | M5 tee nut |  |  | M5 tee nut
2 |  |  | M5 tee nut |  |  | M5 tee nut
2 |  |  | M5 tee nut |  |  | M5 tee nut
2 |  |  | M5 tee nut |  |  | M5 tee nut
2 |  |  | M5x8mm Cap head screw |  |  | M5x8mm Cap head screw
2 |  |  | M5x8mm Cap head screw |  |  | M5x8mm Cap head screw
2 |  |  | M5x8mm Cap head screw |  |  | M5x8mm Cap head screw
2 |  |  | M5x8mm Cap head screw |  |  | M5x8mm Cap head screw
2 |  |  | 252mm GT2 timing belt |  |  | 252mm GT2 timing belt
2 |  |  | M5 tee nut |  |  | M5 tee nut
2 |  |  | M5 tee nut |  |  | M5 tee nut
2 |  |  | M5 tee nut |  |  | M5 tee nut
2 |  |  | M5 tee nut |  |  | M5 tee nut
2 |  |  | M5x12mm Hex head screw |  |  | M5x12mm Hex head screw
2 |  |  | M5x12mm Hex head screw |  |  | M5x12mm Hex head screw
2 |  |  | M5x12mm Hex head screw |  |  | M5x12mm Hex head screw
2 |  |  | M5x12mm Hex head screw |  |  | M5x12mm Hex head screw
2 |  |  | 02 Internal Limit Switch Holder - Left {3D Printed} |  |  | 02 Internal Limit Switch Holder - Left {3D Printed}
2 |  |  | M3 Square nut |  |  | M3 Square nut
2 |  |  | M3x12mm Cap head screw |  |  | M3x12mm Cap head screw
2 |  |  | Microswitch |  |  | Microswitch
2 |  |  | 03 Internal Limit Switch Holder - Right {3D Printed} |  |  | 03 Internal Limit Switch Holder - Right {3D Printed}
2 |  |  | M3 Square nut |  |  | M3 Square nut
2 |  |  | M3x12mm Cap head screw |  |  | M3x12mm Cap head screw
2 |  |  | Microswitch |  |  | Microswitch
2 |  |  | Extrusion 20x40, black anodise, 180mm, one end tap |  |  | Extrusion 20x40, black anodise, 180mm, one end tap
2 |  |  | Double universal L brackets |  |  | Double universal L brackets
2 |  |  | M5x8mm Cap head screw |  |  | M5x8mm Cap head screw
2 |  |  | M5x8mm Cap head screw |  |  | M5x8mm Cap head screw
2 |  |  | Baseplate |  |  | Baseplate
2 |  |  | M5 tee nut |  |  | M5 tee nut
2 |  |  | M5 tee nut |  |  | M5 tee nut
2 |  |  | M5 tee nut |  |  | M5 tee nut
2 |  |  | M5 tee nut |  |  | M5 tee nut
2 |  |  | M5 tee nut |  |  | M5 tee nut
2 |  |  | M5 tee nut |  |  | M5 tee nut
2 |  |  | M5 tee nut |  |  | M5 tee nut
2 |  |  | M5 tee nut |  |  | M5 tee nut
2 |  |  | M5x8mm Cap head screw |  |  | M5x8mm Cap head screw
2 |  |  | M5x8mm Cap head screw |  |  | M5x8mm Cap head screw
2 |  |  | M5x8mm Cap head screw |  |  | M5x8mm Cap head screw
2 |  |  | M5x8mm Cap head screw |  |  | M5x8mm Cap head screw
2 |  |  | M5x8mm Cap head screw |  |  | M5x8mm Cap head screw
2 |  |  | M5x8mm Cap head screw |  |  | M5x8mm Cap head screw
2 |  |  | M5x8mm Cap head screw |  |  | M5x8mm Cap head screw
2 |  |  | M5x8mm Cap head screw |  |  | M5x8mm Cap head screw
2 |  |  | M5x8mm Cap head screw |  |  | M5x8mm Cap head screw
2 |  |  | M5x8mm Cap head screw |  |  | M5x8mm Cap head screw
2 |  |  | M5x8mm Cap head screw |  |  | M5x8mm Cap head screw
2 |  |  | M5x8mm Cap head screw |  |  | M5x8mm Cap head screw
2 |  |  | M5x8mm Cap head screw |  |  | M5x8mm Cap head screw
2 |  |  | M5x8mm Cap head screw |  |  | M5x8mm Cap head screw
2 |  |  | M5x8mm Cap head screw |  |  | M5x8mm Cap head screw
2 |  |  | M5x8mm Cap head screw |  |  | M5x8mm Cap head screw
2 |  |  | Extrusion 20x80, black anodise, 240mm, one end tapped |  |  | Extrusion 20x80, black anodise, 240mm, one end tapped
2 |  |  | Extrusion 20x60, black anodise, 210mm, one end tapped |  |  | Extrusion 20x60, black anodise, 210mm, one end tapped
2 |  |  | 11 Profile Joiner {3D Printed} |  |  | 11 Profile Joiner {3D Printed}
2 |  |  | 11 Profile Joiner {3D Printed} |  |  | 11 Profile Joiner {3D Printed}
2 |  |  | Extrusion 20x80, black anodise, 240mm, one end tapped |  |  | Extrusion 20x80, black anodise, 240mm, one end tapped
2 |  |  | 11 Profile Joiner {3D Printed} |  |  | 11 Profile Joiner {3D Printed}
2 |  |  | 11 Profile Joiner {3D Printed} |  |  | 11 Profile Joiner {3D Printed}
2 |  |  | 2 hole bracket, black |  |  | 2 hole bracket, black
2 |  |  | M5 tee nut |  |  | M5 tee nut
2 |  |  | M5 tee nut |  |  | M5 tee nut
2 |  |  | M5x8mm Cap head screw |  |  | M5x8mm Cap head screw
2 |  |  | M5x8mm Cap head screw |  |  | M5x8mm Cap head screw
2 |  |  | 2 hole bracket, black |  |  | 2 hole bracket, black
2 |  |  | M5 tee nut |  |  | M5 tee nut
2 |  |  | M5 tee nut |  |  | M5 tee nut
2 |  |  | M5x8mm Cap head screw |  |  | M5x8mm Cap head screw
2 |  |  | M5x8mm Cap head screw |  |  | M5x8mm Cap head screw
2 |  |  | 2 hole bracket, black |  |  | 2 hole bracket, black
2 |  |  | M5 tee nut |  |  | M5 tee nut
2 |  |  | M5 tee nut |  |  | M5 tee nut
2 |  |  | M5x8mm Cap head screw |  |  | M5x8mm Cap head screw
2 |  |  | M5x8mm Cap head screw |  |  | M5x8mm Cap head screw
2 |  |  | Extrusion 20x40, black anodise, 100mm, one end tap |  |  | Extrusion 20x40, black anodise, 100mm, one end tap
2 |  |  | Horizontal to vertical profile joiners {3D printed} |  |  | Horizontal to vertical profile joiners {3D printed}
2 |  |  | Horizontal to vertical profile joiners {3D printed} |  |  | Horizontal to vertical profile joiners {3D printed}
2 |  |  | Horizontal to vertical profile joiners {3D printed} |  |  | Horizontal to vertical profile joiners {3D printed}
2 |  |  | M5x8mm Cap head screw |  |  | M5x8mm Cap head screw
2 |  |  | M5x8mm Cap head screw |  |  | M5x8mm Cap head screw
2 |  |  | 06 Top Front Edge {3D Printed} |  |  | 06 Top Front Edge {3D Printed}
2 |  |  | M5x8mm Cap head screw |  |  | M5x8mm Cap head screw
2 |  |  | M5x8mm Cap head screw |  |  | M5x8mm Cap head screw
2 |  |  | M5x8mm Cap head screw |  |  | M5x8mm Cap head screw
2 |  |  | M5x8mm Cap head screw |  |  | M5x8mm Cap head screw
2 |  |  | M5x8mm Cap head screw |  |  | M5x8mm Cap head screw
2 |  |  | M5x8mm Cap head screw |  |  | M5x8mm Cap head screw
1 |  | Barrel Assembly
2 |  |  | 00 Base {3D Printed} |  |  | 00 Base {3D Printed}
2 |  |  | M3 Square nut |  |  | M3 Square nut
2 |  |  | M3 Square nut |  |  | M3 Square nut
2 |  |  | M3x10mm Cap head screw |  |  | M3x10mm Cap head screw
2 |  |  | M3x10mm Cap head screw |  |  | M3x10mm Cap head screw
2 |  |  | Tube 12mm OD, 11mm ID - 324mm (inner barrel) |  |  | Tube 12mm OD, 11mm ID - 324mm (inner barrel)
2 |  |  | Tube 12mm OD, 11mm ID - 380mm (outer barrel) |  |  | Tube 12mm OD, 11mm ID - 380mm (outer barrel)
2 |  |  | Tube 12mm OD, 11mm ID - 380mm (outer barrel) |  |  | Tube 12mm OD, 11mm ID - 380mm (outer barrel)
2 |  |  | Tube 12mm OD, 11mm ID - 380mm (outer barrel) |  |  | Tube 12mm OD, 11mm ID - 380mm (outer barrel)
2 |  |  | Tube 12mm OD, 11mm ID - 380mm (outer barrel) |  |  | Tube 12mm OD, 11mm ID - 380mm (outer barrel)
2 |  |  | Tube 12mm OD, 11mm ID - 380mm (outer barrel) |  |  | Tube 12mm OD, 11mm ID - 380mm (outer barrel)
2 |  |  | Tube 12mm OD, 11mm ID - 380mm (outer barrel) |  |  | Tube 12mm OD, 11mm ID - 380mm (outer barrel)
2 |  |  | 01 Ring 3 {3D Printed} |  |  | 01 Ring 3 {3D Printed}
2 |  |  | 02 Ring 2 {3D Printed} |  |  | 02 Ring 2 {3D Printed}
2 |  |  | 03 Ring 1 {3D Printed} |  |  | 03 Ring 1 {3D Printed}
2 |  |  | 04 End Cap {3D Printed} |  |  | 04 End Cap {3D Printed}
2 |  |  | 05 Centre End Cap {3D Printed} |  |  | 05 Centre End Cap {3D Printed}
2 |  |  | 06 Nozzles {3D Printed} |  |  | 06 Nozzles {3D Printed} | https://github.com/neilbirtles/WaterAutoTurret/blob/main/3D%20Printable%20Parts/Turret%20Barrel/06%20Nozzles.stl
1 |  | Barrel Mount Assembly
2 |  |  | Extrusion 20x20, black anodise, 150mm, no tap {Base} |  |  | Extrusion 20x20, black anodise, 150mm, no tap {Base}
2 |  |  | Extrusion 20x80, black anodise, 150mm, M5 tap both ends {Base} |  |  | Extrusion 20x80, black anodise, 150mm, M5 tap both ends {Base}
2 |  |  | 11 Profile Joiner {3D Printed} |  |  | 11 Profile Joiner {3D Printed}
2 |  |  | 11 Profile Joiner {3D Printed} |  |  | 11 Profile Joiner {3D Printed}
2 |  |  | M5 tee nut |  |  | M5 tee nut
2 |  |  | M5 tee nut |  |  | M5 tee nut
2 |  |  | M5 tee nut |  |  | M5 tee nut
2 |  |  | M5 tee nut |  |  | M5 tee nut
2 |  |  | Inside hidden corner bracket |  |  | Inside hidden corner bracket
2 |  |  | Inside hidden corner bracket |  |  | Inside hidden corner bracket
2 |  |  | M5 tee nut |  |  | M5 tee nut
2 |  |  | M5 tee nut |  |  | M5 tee nut
2 |  |  | 5 Hole T Joining Plate, black anodise |  |  | 5 Hole T Joining Plate, black anodise
2 |  |  | M5x10mm Cap head screw |  |  | M5x10mm Cap head screw
2 |  |  | M5x10mm Cap head screw |  |  | M5x10mm Cap head screw
2 |  |  | M5x10mm Cap head screw |  |  | M5x10mm Cap head screw
2 |  |  | 5 Hole T Joining Plate, black anodise |  |  | 5 Hole T Joining Plate, black anodise
2 |  |  | M5x10mm Cap head screw |  |  | M5x10mm Cap head screw
2 |  |  | M5x10mm Cap head screw |  |  | M5x10mm Cap head screw
2 |  |  | M5x10mm Cap head screw |  |  | M5x10mm Cap head screw
2 |  |  | M5 tee nut |  |  | M5 tee nut
2 |  |  | M5 tee nut |  |  | M5 tee nut
2 |  |  | M5 tee nut |  |  | M5 tee nut
2 |  |  | M5 tee nut |  |  | M5 tee nut
2 |  |  | 06 Extrusion End Cap {3D Printed} |  |  | 06 Extrusion End Cap {3D Printed}
2 |  |  | 06 Extrusion End Cap {3D Printed} |  |  | 06 Extrusion End Cap {3D Printed}
2 |  |  | 06 Extrusion End Cap {3D Printed} |  |  | 06 Extrusion End Cap {3D Printed}
2 |  |  | 07 Extrusion End Cap - Named {3D Printed} |  |  | 07 Extrusion End Cap - Named {3D Printed}
2 |  |  | Extrusion 20x20, black anodise, 90mm, M5 tap one end {Left Support} |  |  | Extrusion 20x20, black anodise, 90mm, M5 tap one end {Left Support}
2 |  |  | M5 tee nut |  |  | M5 tee nut
2 |  |  | M5 tee nut |  |  | M5 tee nut
2 |  |  | M5x10mm Cap head screw |  |  | M5x10mm Cap head screw
2 |  |  | M5x10mm Cap head screw |  |  | M5x10mm Cap head screw
2 |  |  | Extrusion 20x20, black anodise, 90mm, M5 tap one end {Right Support} |  |  | Extrusion 20x20, black anodise, 90mm, M5 tap one end {Right Support}
2 |  |  | M5 tee nut |  |  | M5 tee nut
2 |  |  | M5 tee nut |  |  | M5 tee nut
2 |  |  | M5x10mm Cap head screw |  |  | M5x10mm Cap head screw
2 |  |  | M5x10mm Cap head screw |  |  | M5x10mm Cap head screw
2 |  |  | 04 Barrel Microswitch Mount - Front {3D Printed} |  |  | 04 Barrel Microswitch Mount - Front {3D Printed}
2 |  |  | M3 Square nut |  |  | M3 Square nut
2 |  |  | M3x14mm Cap head screw |  |  | M3x14mm Cap head screw
2 |  |  | 05 Barrel Microswitch Mount - Rear {3D Printed} |  |  | 05 Barrel Microswitch Mount - Rear {3D Printed}
2 |  |  | M3 Square nut |  |  | M3 Square nut
2 |  |  | M3x14mm Cap head screw |  |  | M3x14mm Cap head screw
2 |  |  | Microswitch |  |  | Microswitch
2 |  |  | Microswitch |  |  | Microswitch
2 |  |  | 00 Left Bearing Housing {3D Printed} |  |  | 00 Left Bearing Housing {3D Printed}
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

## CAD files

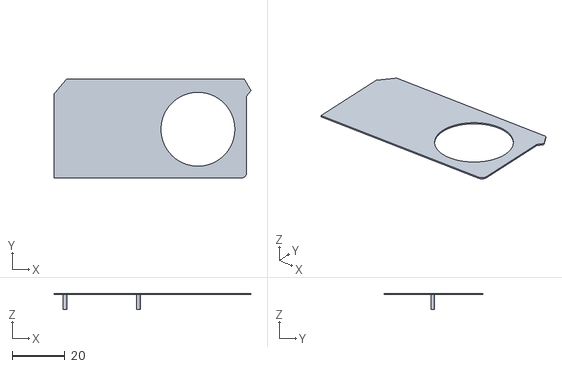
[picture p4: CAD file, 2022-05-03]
3D Printable Parts/Electronics Enclosure/08 Heatsink Insulator.stl
74.7 x 37.6 x 6.13

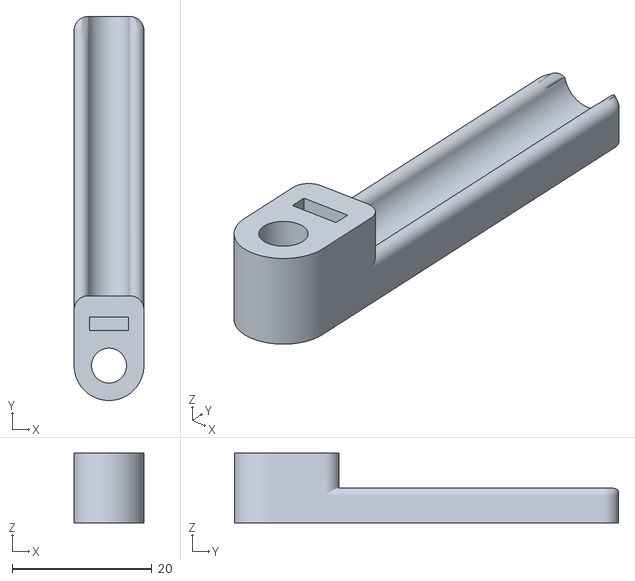
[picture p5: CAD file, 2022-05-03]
3D Printable Parts/Internal Bearing and Motor Mount/02 Limit Switch Arm - Internal.stl
10.0 x 55.0 x 10.0

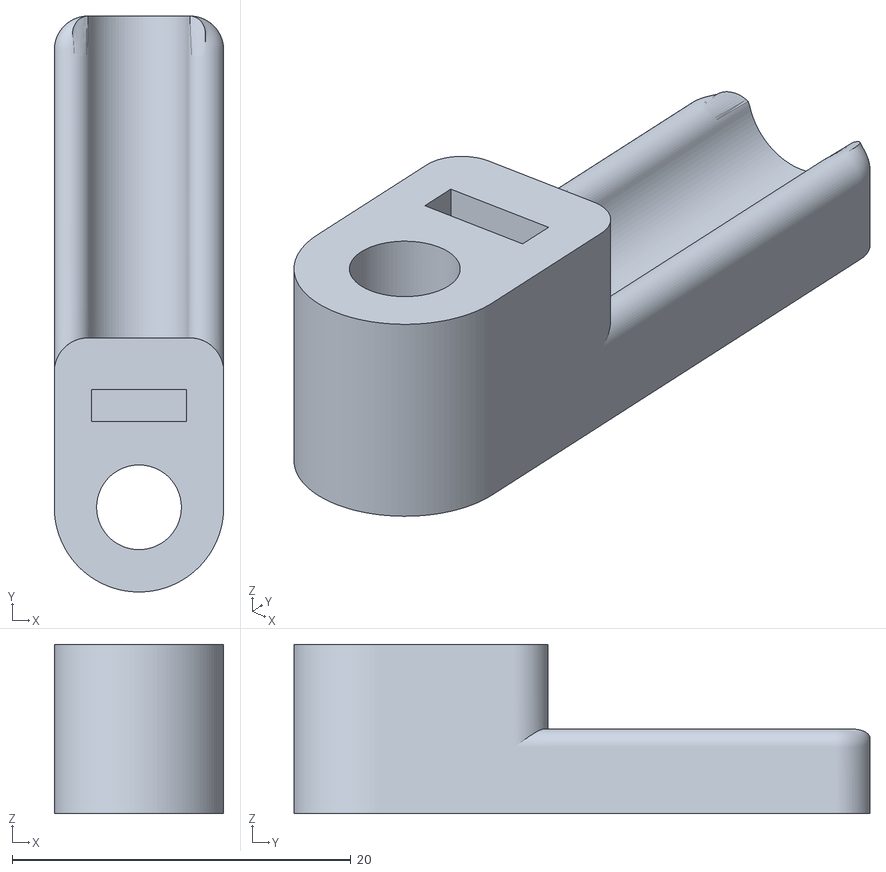
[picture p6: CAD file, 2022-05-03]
3D Printable Parts/Turret Barrel Mount/10 Limit Switch Arm - Barrel.stl
10.0 x 34.0 x 10.0

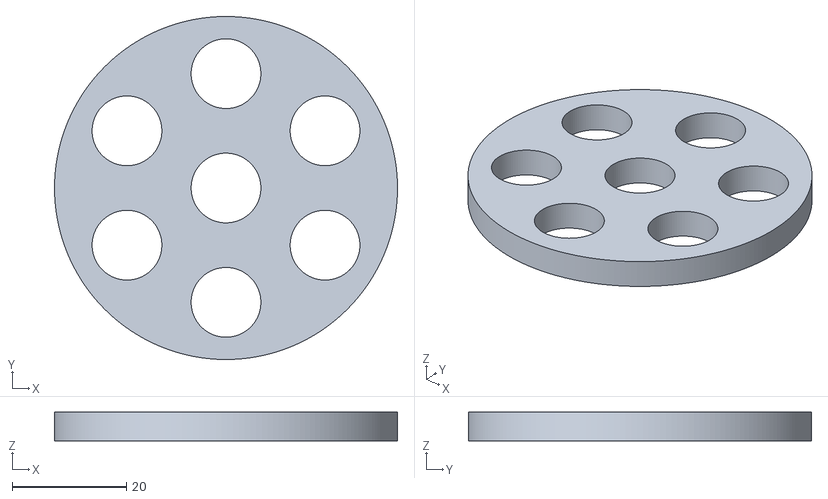
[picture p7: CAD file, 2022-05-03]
3D Printable Parts/Turret Barrel/03 Ring 1.stl
60.0 x 60.0 x 5.00

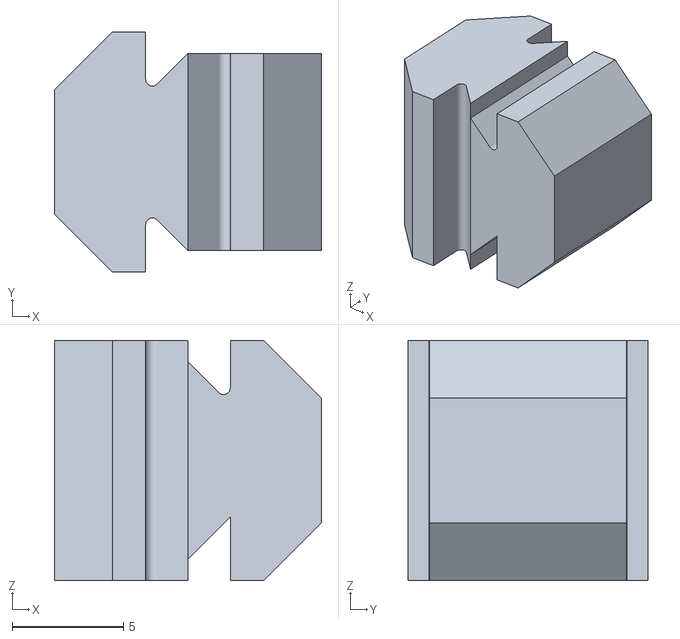
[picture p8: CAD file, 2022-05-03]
3D Printable Parts/Turret Base/11 Profile Joiner - Horiz to Vert.stl
12.0 x 10.8 x 10.8

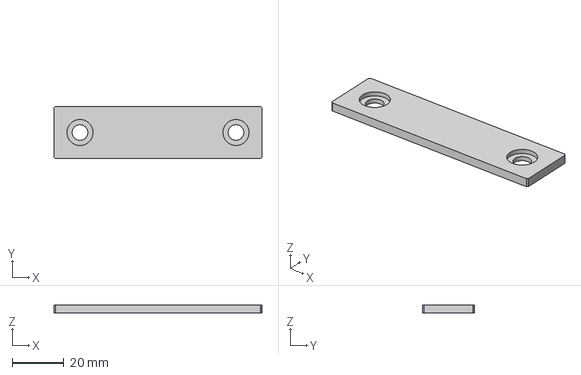
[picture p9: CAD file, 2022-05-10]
Fusion360 Files/Extrusion-End-Cap-20x80_v1.step
80.0 x 20.0 x 3.00 mm

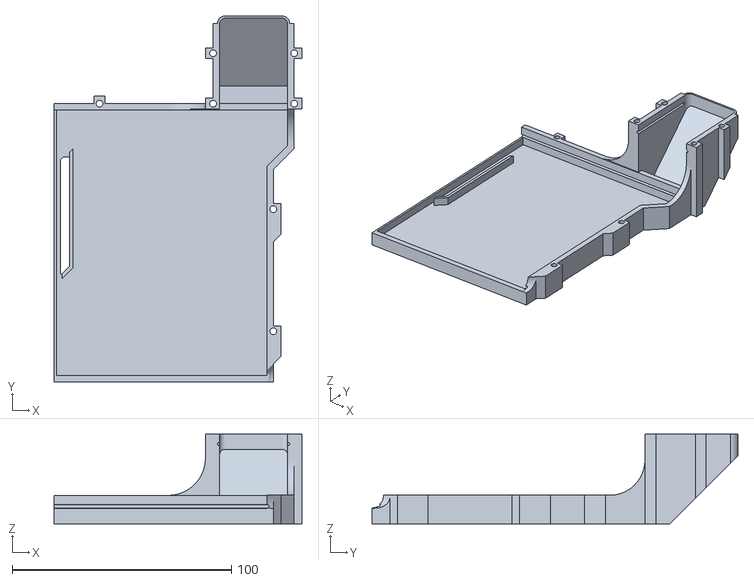
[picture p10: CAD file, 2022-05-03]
3D Printable Parts/Electronics Enclosure/01 Electronics Enclosure Lid.stl
113.0 x 167.0 x 40.9

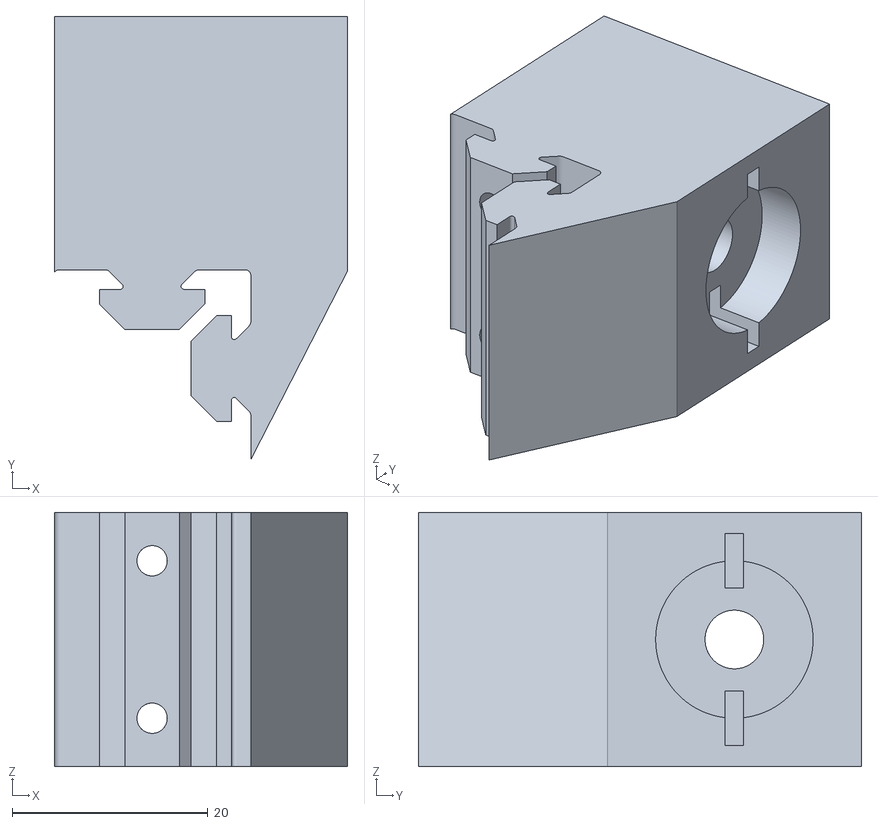
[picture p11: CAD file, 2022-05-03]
3D Printable Parts/Internal Bearing and Motor Mount/00 Bearing Mount.stl
30.0 x 45.3 x 26.0

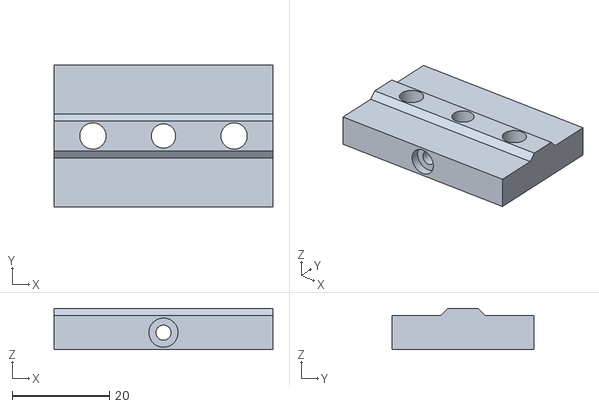
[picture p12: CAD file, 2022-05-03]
3D Printable Parts/Turret Barrel Mount/08 Barrel Mount Rotary Attachment.stl
45.0 x 29.1 x 8.49

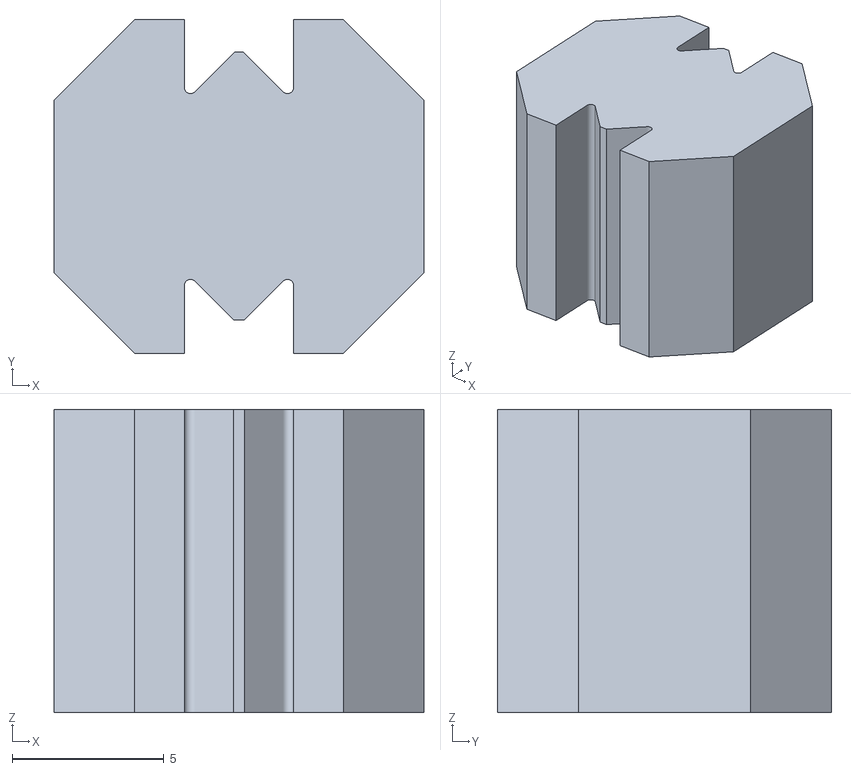
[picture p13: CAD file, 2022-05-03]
3D Printable Parts/Turret Base/10 Profile Joiner.stl
12.2 x 11.0 x 10.0

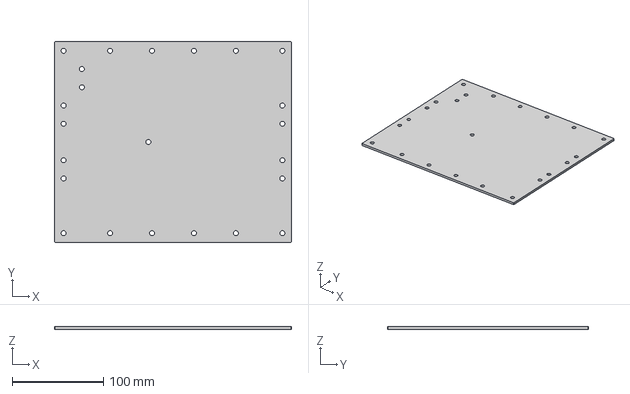
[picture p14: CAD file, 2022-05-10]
Fusion360 Files/Baseplate_v9.step
260.0 x 220.0 x 3.00 mm

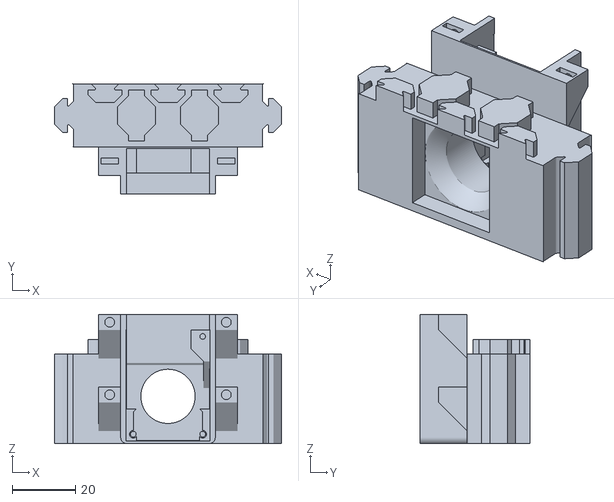
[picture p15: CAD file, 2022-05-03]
3D Printable Parts/Electronics Enclosure/02 Camera Enclosure.stl
72.0 x 35.0 x 41.0

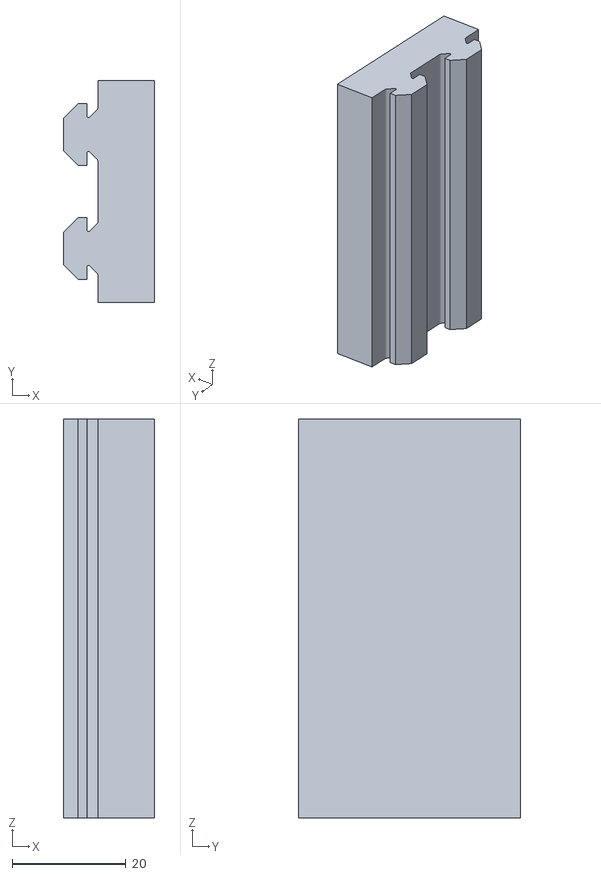
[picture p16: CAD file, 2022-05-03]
3D Printable Parts/Internal Bearing and Motor Mount/01 Battery Top Spacer.stl
16.0 x 39.0 x 70.0

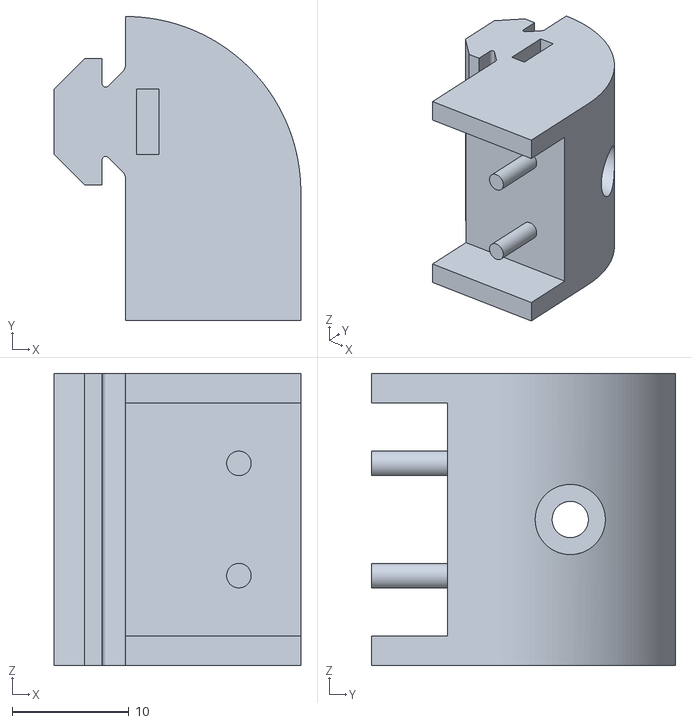
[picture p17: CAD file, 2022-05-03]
3D Printable Parts/Turret Barrel Mount/04 Barrel Microswitch Mount - Front (Supports Needed).stl
21.1 x 26.0 x 25.0

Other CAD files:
3D Printable Parts/Turret Barrel/02 Ring 2.stl
3D Printable Parts/Turret Barrel/04 End Cap.stl
3D Printable Parts/Turret Base/05 Top Rear Edge.stl
Fusion360 Files/2060_Simple_v5.step
3D Printable Parts/Electronics Enclosure/00 Electronics Enclosure Base (Supports Needed).stl
3D Printable Parts/Electronics Enclosure/03 Camera Enclosure Window Frame.stl
3D Printable Parts/Electronics Enclosure/04 Top Right Spacer.stl
3D Printable Parts/Electronics Enclosure/05 Bottom Right Spacer.stl
3D Printable Parts/Electronics Enclosure/06 Bottom Left Spacer.stl
3D Printable Parts/Electronics Enclosure/07 Top Left Spacer.stl
3D Printable Parts/Turret Barrel Mount/00 Left Bearing Housing.stl
3D Printable Parts/Turret Barrel Mount/01 Left Bearing Housing - Cap.stl
3D Printable Parts/Turret Barrel Mount/02 Right Bearing Housing.stl
3D Printable Parts/Turret Barrel Mount/03 Right Bearing Housing - Cap.stl
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

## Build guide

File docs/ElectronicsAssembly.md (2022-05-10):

# Electronics Assembly
## Water Auto Turret Controller Board Assembly
The PCB has been designed to be relatively easy to assembly - only two surface mount components have been used - solenoid driver DRV8806 (only available in surface mount) and the power connector to join to the VIM3 (was easier to buy the khadas VIN to VIN Cable and solder this power connector on than it was to crip the cables to go into the connector on the VIM3!). Both these surface mount components can be hand soldered but the DRV8806 also has a thermal pad underneath it that means its easier to solder this with paste and hot air but it can be done with past and a soldering iron as there are a number of vias through to the VSS plane on the rear of the board. The power connector can just be tacked on one pin then aligned and then the rest can be soldered. The rest of the components are through hole and can be assembled in the normal size based order paying attention to orientation of polarised devices like diodes and capacitors. All components go on the top side of the board apart from the 40pin header socket that goes on the under side of the board to allow it to join to the VIM3 - I added this header after the surface mount components we soldered on to allow easy access to the pins for soldering. The TMC5160 breakout boards are mounted in pin header sockets for easy insertion / removal as two of the mounting screws are under these boards. This also has the added benefit of providing more space for mounting components and some resistors that were originally missed off have been mounted under them. Pay attention to the way these are mounted on the main board - the motor outputs (labeled A1, A2, B1 and B2), but do not mount them yet as the board needed to be assembled into the Electronics Enclosure first.

A few errors were found in the rev 1 Water Auto Turret Controller Board that needed modifications to be made - these were fixed in the rev 2 PCB and are listed below for information:
* SPI chip select was driven by an AND gate as i mistakenly believed you needed to use the CS pin that was part of the SPI port on the VIM3 for controlling CS and so the design had this CS pin (pin 15) wired into one input on each AND gate in a dual AND gate chip with two other GPIO pins used to drive the other inputs on the AND gates, with one motor controller on each of the AND gate outputs. The intention of using the GPIO pins to select which AND gate output would become active when the CS pin was activated. Having started coding it turns out this was completely not needed and I could just use the GPIO pins as the SPI CS pins directly. The rev 1 board was modded to break the link to Pin 15 and just pull these two inputs to +3v3, effectively making the AND gates pass through for the other GPIO pin levels. The rev 2 board removed this AND chip and linked the SPI CS on the motor drivers directly to the GPIO pins (WiringPi pin 7 or physical GPIO pin 23 for the pitch motor and WiringPi pin 6 or physical GPIO pin 22 for the yaw motor).
* Added pull up resistors to the REFL and REFR pin on both the motor controller boards that were missed off in the original design
* Added header for plugging in the enclosure fan 
* Added pull up resistor for the charging input sense line - the microcontroller has weak internal pull ups but option for external pull up added as well in case its needed
## Electronics Enclosure Assembly 
Refer to the Equipment Breakdown Structure for the items required to assemble the electronics enclosure.
### Camera Enclosure 
The first part to prepare is the 3D printed {02 Camera Enclosure}. The diagram below shows this part. 

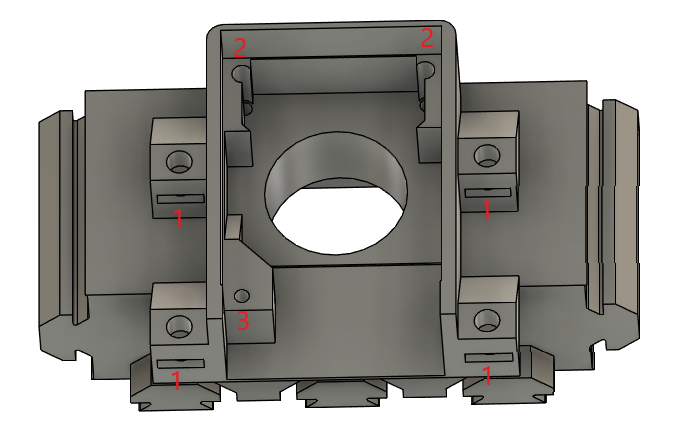
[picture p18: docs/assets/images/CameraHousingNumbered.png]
Camera Housing


First on the Camera Enclosure is to insert the 4 M3 square nuts into the slots marked 1 and press them home until the threads in the nuts line up with the holes above them. Ive found the easiest way to do this is to use needle nose pliers to hold them and push them part way in and then adjust grip and push them flush with the edge of the pliers. 

Next up is to mount the Khadas OS08A10 8MP HDR Camera itself. This should fit easily with the lens poking through the big round hole and the cable coming out the back of the Camera Enclosure (at the end near the hole marked 3). To fix the camera in place use M2x16mm screws in the two holes marked (2) and an M2x6mm screw in the hole marked (3).

On the other side of the Camera Enclosure the 25x25x3mm acrylic window (sourced from an online laser cutting service) and {03 Camera Enclosure Window Frame} need to be fitted. The acrylic window is put into place, glue is added round the frame to make a waterproof seal (super glue can be used but beware of frosting of the window) and then the window frame is added over the top to finish the look off.

This is the Camera Enclosure finished.

### Electronics Enclosure Base
The diagram below shows the 3D printed {00 Electronics Enclosure Base}. The area marked 7 is the air plenum - before assembly ensure that this area is free of support material. There should be none due to the design with the use of max 45 degree angles but it is easiest to clear now if any are present.

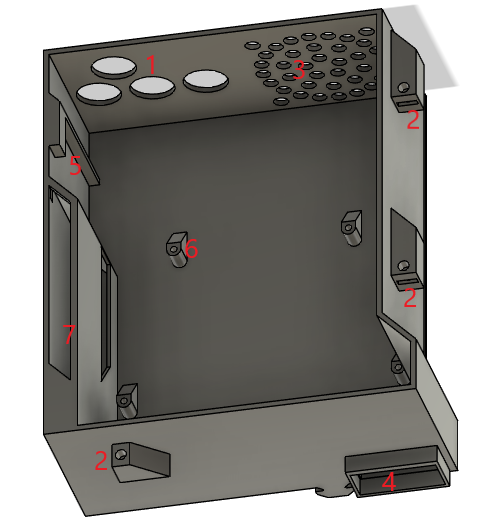
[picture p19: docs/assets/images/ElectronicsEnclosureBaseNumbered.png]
Electronics Enclosure Base


First insert the 4 grommets into the holes in the Electronics Enclosure (1) - this can be a bit fiddly to get them in but they do fit! Next insert the square nuts into the slots (2) in the 3 lid fixing points. Next the fan is added - it is mounted on the internal face ensuring that the air flow direction is exhausting out of the case. Fix the fan in place using 4 M4x14mm screws from inside the enclosure to 4 hex nuts on the outside. Align the wire so that it be easily routed over the opposite corner of the enclosure as this is where the header is to plug it in - note that this will have to route over top of the controller board once it is installed as there are no gaps between the controller board and the edge of the case. Attach a pin header socket to the end of the wire from the fan (trimming to length if needed), the fan for the turret base also needs to be crimped into this connector and so the wire needs to be pulled through one of the grommets before crimping in.

Next it’s time to prep the Khadas VIM3 - note that it is easiest to do the basic OS setup and the required image must be flashed before installing in the case, otherwise the serial debug link has to be used as there is no access to the USB-C or ethernet ports when it's in the Electronics Enclosure. See the Software Setup for this initial configuration.

On the VIM3 remove the bluetooth antenna as it is not needed. Next install the heatsink and fan as per the instructions. And finally plug one end of the VIN to VIN cable into the socket on the bottom of the VIM3 (on the opposite side of the PCB to the USB-C port). WIth these items in place now take the Camera Enclosure and align it so that cable from the camera goes through the slot in the Electronics Enclosure Base (4). Now the cable from the camera can be plugged into the MIPI-CSI socket on the bottom of the VIM3 ensuring the orientation is as per the picture [here](https://docs.khadas.com/linux/vim3/MIPICamera.html) and being careful not to put too much stress on the cable as they can tear relatively easily when not completely flat and the cable has a gentle bend in to fit in this design. The VIM3 can now be placed in the Electronics Enclosure Base with the mounting holes lined up with the supports in the base (6) - again being careful of the camera cable in this step. Next the heatsink insulator and spacers are added (yellow items in the following diagram). It can be useful to use a dab of superglue on the spacers to hold them in place during assembly.

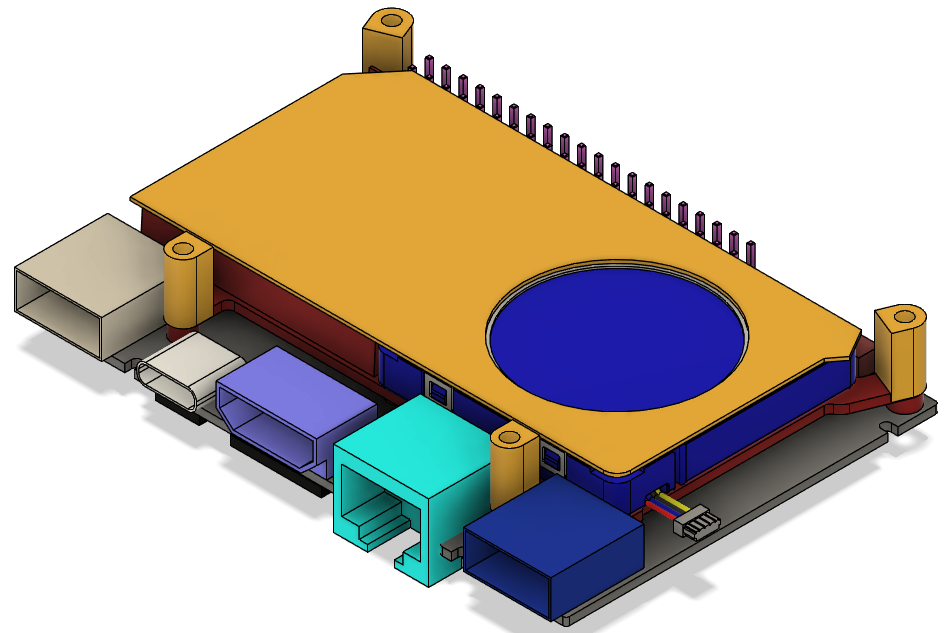
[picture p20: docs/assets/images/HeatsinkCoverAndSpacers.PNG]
Heatsink and Spacers


With these items in place the Water Auto Turret Controller Board can be plugged into the VIM3 by mating the 40 way GPIO header on the VIM3 and the socket on the bottom of the Water Auto Turret Controller Board. This can be relatively tricky and again be careful of the camera cable in this step. Once assembled then both boards are screwed into mounting points (6) on the Electronics Enclosure base using 4 M2x18mm screws. To aid installation the Water Auto Turret Controller Board PCB will be approximately flush with the the front (side near (4)) and left (side near (7)) side of the Electronics Enclosure Base. Once installed then the VIM3 Wifi antenna can be pushed into its mounting hole (5). The TMC5160 breakout boards can now be installed. Pay attention to the way these are mounted on the main board - the motor outputs (labeled A1, A2, B1 and B2).

With this assembly complete both the Electronics Enclosure Base and Camera Enclosure can be slid into the Turret Base front panel making sure that the parts that slide into the extrusions are lined up so that the Camera Enclosure fits into the gap in the top middle of the front panel. With the Camera Enclosure pushed all the way home it should be slightly below the top of the extrusions. The Electronics Enclosure Base should be pressed as close to the Camera Enclosure as possible so that the lip on the top of it (4) sits inside the bottom of Camera Enclosure. Correct positioning can be checked by test fitting the Electronics Enclosure lid and making sure all screws line up with the nuts in the Electronics Enclosure Base and Camera Enclosure.

### Wiring
The wiring for the Water Auto Turret is pretty straight forward, just need to follow it through in sequence and double check connections. The image below shows the connector locations on the Water Auto Turret Controller Board for ease of reference during assembly. When measuring wiring it is useful to allow it to be long enough for the front panel of the turret base to be laid flat in front of the turret to allow for ease of assembly / maintenance.

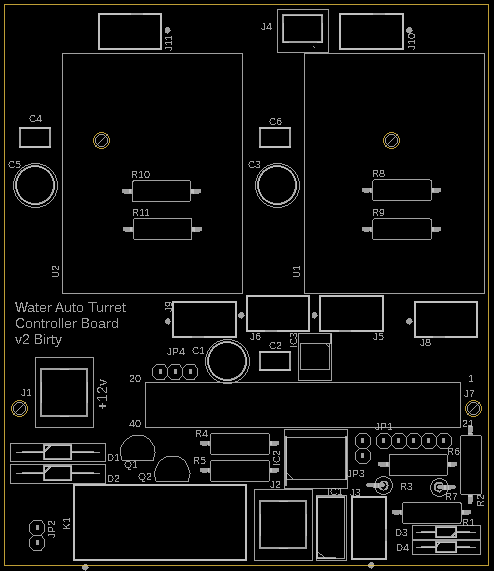
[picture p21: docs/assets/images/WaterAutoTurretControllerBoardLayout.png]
Controller Board Layout


#### Solenoids
The solenoid valves need connections to each coil, but the polarity does not matter so does not have to be tracked. The solenoid valve connections are designed for push on spade connectors, but they can also be soldered on if required. These wires need to be long enough to reach J5 and J6 on the controller board - it does not matter which solenoid joins to which connector and both connectors have the same pinout - pins 1 and 2 are for one solenoid and pins 3 and 4 are for the other. The wires from the solenoid should be threaded through the grommet and then have ther ends crimped into the pins which are then inserted into the connector housing. Getting the correct crimp tool and make this much easier but it can be done with needle nose pliers with practice!

#### Limit Switches
There are 4 limit switches used in the design, 2 for the yaw motor (mounted inside the turret base) and 2 for the pitch motor (mounted on the barrel mount). Again polarity does not matter. The yaw limit switches join to connector J8 and the pitch limit switches join to connector J9. The pinout for both these connectors is the same with pins 1 and 2 for the left reference input and pins 3 and 4 for the right reference input. I found it helpful to wire the switches up so that on the yaw the left switch is triggered when the barrel is at its left most extreme when looking from the back of the turret (similar for the right switch) as this then aligns with the perspective from the camera. The pitch ones matter less so wire however makes sense. 

One end of the limit switches wires are soldered to the normally open microswitch connections and then routed through the turret in such a way that they will not get tangled in any moving parts (I used sticky back cable tie holders and cable ties for this job), in through one of the grommets (I shared a grommet between the motor wiring and the limit switches for that motor but it doesn't really matter) and then the other ends are crimped into pins and inserted into the connector housing. 

The wiring from the pitch limit switches (along with the wiring for the pitch motor) needs to be routed down one of the non-water carrying pipes that join onto the barrel. This is simply done by cutting a slit in the tube and passing the cables down before routing internally as above.
#### Motors
The stepper motors already have connectors on, however the wiring is too long and so these connectors can be cut off to make for easier routing and installation. 

The wiring from the pitch motor needs to be fed down one of the pipes (as above with the microswitches) and then routed internally, then through one of the grommets, crimped into pins, inserted into the connector housing and then connected to J11. The pinout for this connector is pin 1 and 2 for coil 1 and pin 3 and 4 for coil 2. The polarity of the coils and which coil is on which set of pins does not matter. If it is not known which wires from the motor join to which coil then this can be discovered using a multimeter - with the two wires for a coil giving a low resistance and wires for unrelated coils giving open circuit. 

The wiring for the yaw motor is just routed internally and joined onto connector J10. The pinout for this connector is the same as J11. 
#### Indicators 
Next up is to connect up the dual colour LED and the charging sense wire from the power and water inlet 3D printed part. 4 wires are used to link these items, 3 wires for the 3 pins on the LED and one wire linked to the sleeve shunt on the power inlet connector (this sleeve shunt is normally connected to the sleeve (i.e. 0v) until a power connector is plugged in at which point this becomes open circuit and so allows detection of the charging plug being inserted). These wires need to be routed internally again, through the grommet and onto J3. The pinout for this connector is 1 - Green LED, 2 - Red LED, 3 - LED common, 4 - power sense
#### Power Wiring
The final wiring needed is to wire up the power cabling. Relatively thick cable has been used to carry the currents present in the system with the stepper motors and solenoids all potentially powered at the same time. The diagram below shows the connections required.

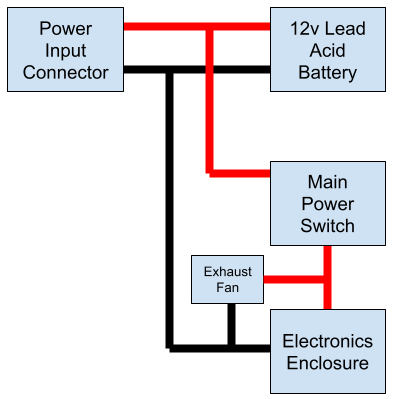
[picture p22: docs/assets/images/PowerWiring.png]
Power Wiring


The power input connector is used to allow charging of the battery when it is installed in the enclosure. The exhaust fan is used to prevent buildup of gasses inside the enclosure when charging - its after the power switch to allow it to be turned on and off, the sense wire in the electronics prevents the system from being used when the battery is charging.

All power wires have terminals crimped onto them to allow connections to be made. Where there are two power wires joined (e.g. wires from the power input connector to the battery and to the mains power switch) then the terminals on the battery are used to stack them as there is the most room there. The following are the termination types for each cable:
* Power Input Connector (solder) => 12v Lead Acid Battery (ring terminal) {both red and black}
* 12v Lead Acid Battery (ring terminal) => Main Power Switch (spade terminal) {red}
* 12v Lead Acid Battery (ring terminal) => Electronics Enclosure (ring terminal) {black}
* Main Power Switch (spade terminal) => Electronics Enclosure (ring terminal) {red}
* Exhaust fan - crimped into the same connector as the fan for the Electronics Enclosure.
### Testing
Once all the wiring has been completed then the system can be powered up for a test to ensure it all works before fixing the lid. The sequence following engaging the main power switch should be as follows - green led will come on, red led will light, relay will click then the VIM3 fan will be heard to start, after a time for bootup it should be possible to log-in to the VIM3. The motor homing test software can then be run to test the motor and limit switch connections. Then the solenoid test software can be run to test those connections. If everything works then shutdown the VIM3 and power off, if not then check connections and repeat until it is all functioning correctly.
### Electronics Enclosure Lid 
Once all testing is complete and passed then the final step is to add the lid. The Electronics Enclosure Lid (see diagram below) simply needs some O-ring to be fixed in place in the grove (1) around the inside edge. I simply used green threadlock to hold this in place as I had it, but any glue that wont attack the rubber O-ring can be used. Once the O-ring glue is set then the lid can be placed on the Electronics Enclosure. The screws used to fix the lid in place are as follows 3 M3x20mm (2), 2 M3x50mm (3) and 2 M3x35 (4) inserted from the opposite side to shown in the diagram below.

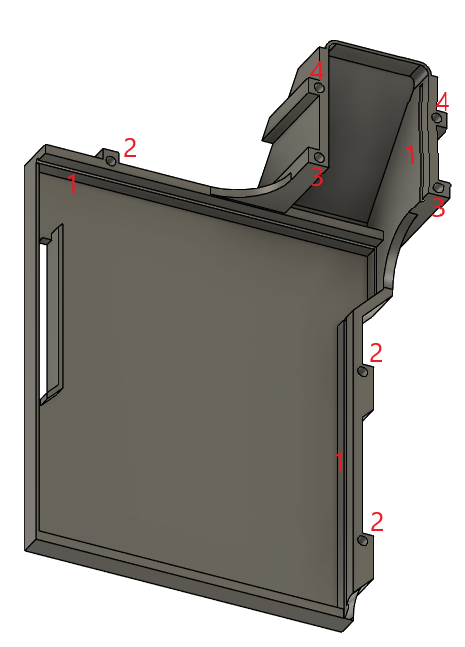
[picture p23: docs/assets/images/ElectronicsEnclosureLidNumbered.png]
Electronics Enclosure Lid


## Final Assembly 
With all the components now wired in the battery can be slid into place in the turret base and the battery side support can be put in place using three horizontal to vertical profile joiners and two M5x8mm screws into the bottom of it through the baseplate. 

The Turret Base front panel can now be installed. The {06 Top Front Edge} needs to be put on the top of the front panel and then the front panel can be offered up to the rest of the Turret Base and then can be screwed in with 6 M5x8mm screws through the baseplate. 

That completes the assembly of the Water Auto Turret!

[{Home}](README.md)

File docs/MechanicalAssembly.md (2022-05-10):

# Mechanical Assembly

There are a number of sub assemblies to construct that are then assembled into the overall water turret. There is no fixed order that these sub assemblies need to be built in however we are going to start with the Internal Bearing and Motor Mount. There are separate Fusion360 models for each of these sub assemblies to aid assembly. 3D printed parts has been {} to allow for easy identification e.g. {00 Bearing Mount}

## Internal Bearing and Motor Mount
Refer to the Equipment Breakdown Structure to identify the list of part required for this sub assembly.

The diagram below shows the major items and how they fit together for the internal bearing and motor mount.

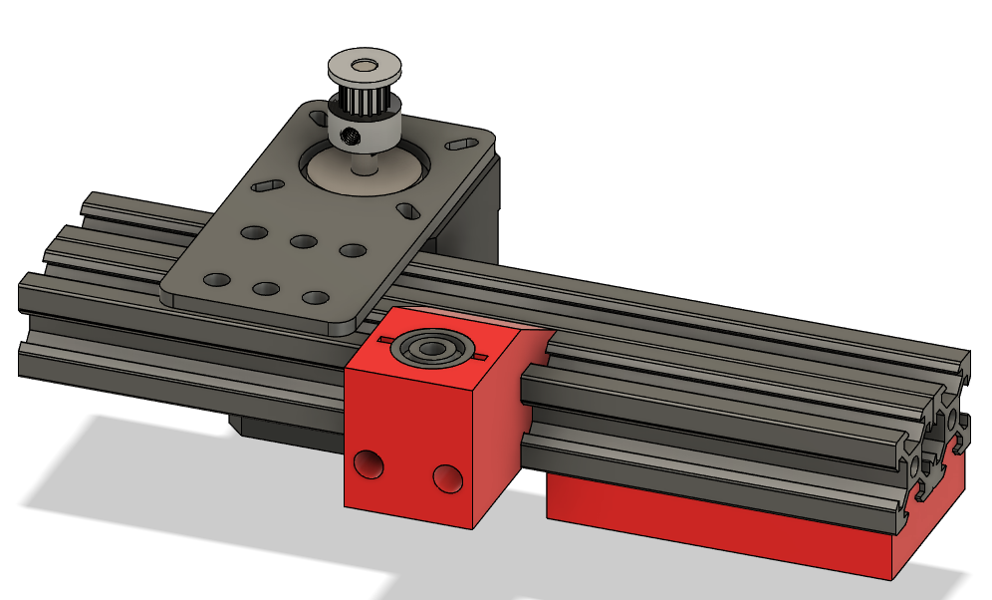
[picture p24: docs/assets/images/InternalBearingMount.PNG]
Internal Bearing and Motor Mount


First take the {00 Bearing Mount} and insert the two M3 square nuts into the slots on the top and push down until the thread of the nut is aligned with the holes for the two M3x25mm screws that are on the front. This should simply require pushing the nuts down as far as they will do with a suitable tool, e.g. needle nose pliers. Once pushed in the insert the M3x25mm screws but not far enough to protrude from the Bearing Mount on the shape that slides into the aluminum extrusion. These screws are for locking the Bearing Mount in place against the extrusion to prevent it moving and so will be tightened in a later step. Next insert the two 625ZZ bearings into the round holes on the top and bottom of the Bearing Mount.These should be tight friction fits and if they are not then a dab of glue can be used to hold them in place (remembering not to get any in the bearing itself).

The Bearing Mount is then slid onto one side of the 20x40x150mm aluminum extrusion and positioned exactly in the middle - there should be 76mm either side of the {00 Bearing Mount} to the ends of the extrusion. Getting this exactly in the middle is important as this bearing holds the yaw shaft for the barrel. Once it is in place then tighten the M3x25mm screws in the front of the Bearing Mount until there is strong resistance to the part moving in the extrusion but not too tight or they may crack the 3D printed part. Once the screws are tightened then re-measure to make sure the Bearing Mount is still in the exact centre of the extrusion.

Next slide the {01 Battery Top Spacer} into right hand underside of the aluminum extrusion. The end of the Battery Top Spacer should be flush or slightly in from the right hand end of the extrusion. To aid holding the battery in place a rectangle of 2mm foam needs to be cut and stuck to the underside of the Battery Top Spacer.

The motor now needs to be mounted on the left hand side of the extrusion on the opposite side from the Bearing Mount. First slide two tee nuts into each slot on the extrusion, then place the NEMA17 Motor Bracket over the extrusion and line up the holes in it and the tee nuts in the extrusion. Next use M5x8mm screws to losely bolt the bracket into place. Next use M3x6mm screws to attach the NEMA17 Motor to the bracket. Next the 16 Tooth, 5mm bore, 2GT Pulley is mounted on the shaft of the motor - this should be mounted near the top of the shaft on the motor and be screwed in tight noting that this may need to be adjusted during final assembly.

Two tee nuts need to be inserted one in each of the (bottom) slots in the aluminum extrusions. These are to join the battery front support onto at a later stage of assembly.

The last two items to be fitted are the brackets to join this subassembly to the rest of the turret base - these are not shown in the diagram above. These are two slot, 90 degree brackets. One is fitted on each side the left hand side bracket is fitted under the profile and the right hand side are fitted above the profile. Both are fitted in the same manner - two tee nuts are slid into the profile (one in each slot in the profile), the bracket is placed on top and loosely screwed into place using M5x8mm screws. The brackets will need to be adjusted in the final assembly but need to be tight enough to stop them falling off at this stage!

## Barrel Assembly
Refer to the Equipment Breakdown Structure to identify the list of part required for this sub assembly.

The diagrams below shows the major items and how they fit together for the barrel. A front and rear view is provided to show all the key features.

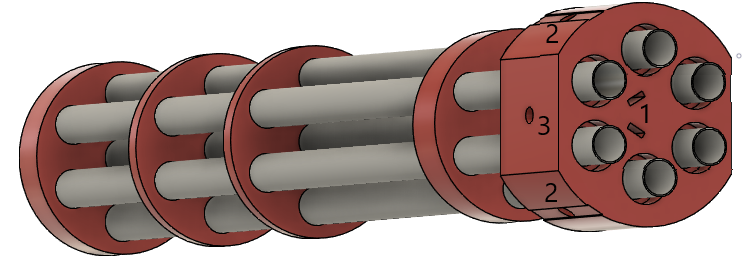
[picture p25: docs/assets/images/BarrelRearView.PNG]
Barrel Rear View


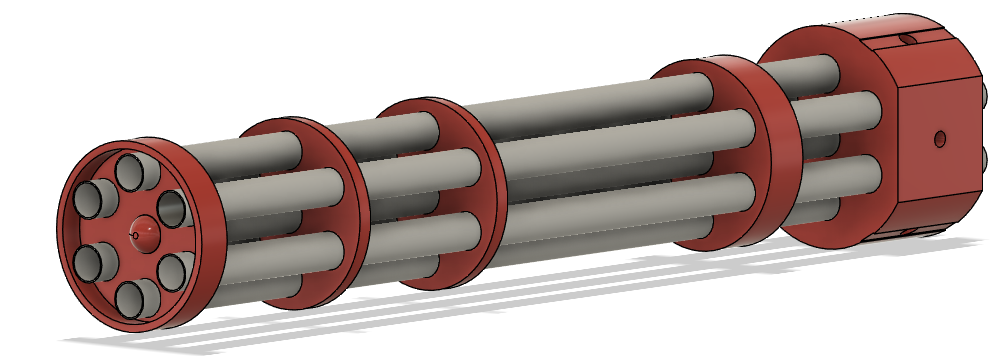
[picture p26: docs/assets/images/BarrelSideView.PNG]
Barrel Side View


Assembly of the barrel starts with the {00 Base} 3D printed part. First two M3 square nuts are inserted into the slots (1) then M3x10mm screws are screwed into the two holes (2). These screws are to lock the barrel on the shaft that goes through the hole in the side (3) and so these screws must not be screwed in too far at this point or it will be impossible to insert the shaft. 

Next to be added is the central plastic barrel (324mm) which must be inserted as far as possible into the base noting that this does not protrude out the other side of the base. Following this two of the outer barrels (380mm) can be inserted into the base on opposite sides of the central barrel. These outer barrels need to protrude 10mm from the back base to provide support to the flexible tubing when it is attached. Once these outer barrels are installed then the barrel rings can be installed, {01 Ring 3} is installed first, then {02 Ring 2}, then {03 Ring 1} and then {04 End Cap}. In the design above the following spacings are used for the rings (measured from the edge of the base nearest the rings to the bottom of the other rings):
* Ring 3 - 45mm
* Ring 2 - 185mm
* Ring 1 - 250mm
* End Cap - 318mm
These spacings are not essential so can be adjusted for how the builder wants to make the barrel look. Once the rings are in place the remaining barrels can be worked into place. Depending on the tolerances of the 3D printer used the use of a rubber mallet may be required to get them all in place!

Once the barrels are all in and adjusted to be level then the nozzles can be fitted. In the current build 3 blank nozzles are fitted in the centre, top and bottom most barrels and the right and left barrels have different size nozzles. The nozzles are simply fixed in place with hot glue, squirt some round the underside of the mating side of the nozzle and push it home. The excess can then be trimmed.

## Barrel Mount Assembly 
Refer to the Equipment Breakdown Structure to identify the list of part required for this sub assembly.

The diagram below show shows the barrel mount assembly with the motor cover removed to show assembly. The first step is to join the two base aluminum extrusions (20x80x150mm both ends tapped and 20x20x15 untapped) together using the two profile joiner pieces which are simply slid into the holes in the profiles. 

Next two tee nuts for mounting the motor to are slid into each of the 2nd and 4th extrusions (top side) slots in the base created above and one right angle hidden corners to support the uprights are slid into each side in the centre extrusion (top side) slot. Two tee nuts are slid into the centre extrusion (bottom side) slot in preparation for attaching the Barrel Rotary Attachment.

The side T-pieces are then screwed into the base profiles using 3 M5x10mm screws in each T-piece. Two tee nuts need to be slid into the 1st and 5th extrusion (bottom side) slots in preparation for attaching the rotary bearing. The {06 Extrusion End Cap} can be fitted onto 3 of the corners and one {07 Extrusion End Cap - Named} can be fitted to the remaining corner (or an additional plain one can be used if preferred). 

The upright extrusions (20x20x90mm one end tapped) are then screwed into place by sliding the upright half of the hidden corner bracket into one side of the profile (with the tapped hole facing upwards) and then sliding it and the bracket over to be flush with the T-piece. Two tee nuts are then inserted into the upright on the side nearest the T-piece and screw in place using M5x8mm screws. Once the screws on the T-piece are in place then the hidden corner bracket grub screws can also be tightened to lock the upright in place. This can then be repeated for the upright on the other side. 

The {04 Barrel Microswitch Mount - Front} and {05 Barrel Microswitch Mount - Rear} need to have one M3 square nut pushed into each of them and one M3x14mm screws can be screwed into each until it is just before the edge touching the profile. They can now be slotted onto the left hand upright and pushed down until approx 2mm below the top of the extrusion paying attention to which is the front and which is the rear. They should be installed as per the diagram below. The microswitches can now be mounted into these with the levers pointing upwards. A dab of glue can be used to hold them in place if needed. The M3x14mm screws can now be tightened down to hold them in place.

The {00 Left Bearing Housing} and {02 Right Bearing Housing} can then be placed on the supports and screwed on with M5x10mm screws. Two 625ZZ bearings are then installed into each of the bearing housing - these should be friction fits but a dab of glue can be used if required to hold them in place. The {00 Left Bearing Housing - Cap} and {02 Right Bearing Housing - Cap} can then be installed on the top of the bearing housings. 

The NEMA23 motor bracket slotted holes need to be widened out using a file to allow for M5 screws and then is screwed down to the base using low profile M5x8mm screws in such a way as to roughly centre the motor on the base with hole for the motor shaft being to the right. These should be tightened to lock this in place. The NEMA23 motor is then screwed into the bracket using 4 M4x10mm screws and 4 M4 hex nuts, ensuring that the wire for the motor comes out the rear  allowing it to be fed through the hole in {11 Top Motor Cover}. The 18 tooth, 6.35mm bore GT2 pulley is put on the motor shaft and tightened in place using its grub screws. Double sided tape can then be put on the top of the motor and the Top Motor Cover can be put in place and pressed down to make it stick to the double sided tape.

On the underside of the base the Barrel Mount Rotary Attachment can now be fitted - this piece provides the clamping mechanism to join the yaw shaft onto the barrel mount. First the {08 Barrel Mount Rotary Attachment} is prepped by putting one M3 square nut into each of the holes on the top and pressing them in until the threads line up with the holes from the sides. One M3x12mm screw is then put in from each side and screwed in until just before the ends enter the central hole (for the yaw shaft). The Barrel Mount Rotary Attachment can now be loosely screwed to the underside of the Barrel Mount using M5x12mm screws mated with the tee nuts that were inserted earlier. The {09 Barrel Mount Rotary Attachment - centre spacer} can then be used to exactly align the Barrel Mount Rotary Attachment in the centre of the barrel mount base by using this to go between the end of the extrusion and the Barrel Mount Rotary Attachment itself. Check this on both sides and once aligned screw down tight but not too tight or the 3D printed part may crack. Next up is the add the yaw shaft itself. A 105mm length of 5mm hardened steel rod is required - to cut this something like a tungsten carbide blade will be required and to put the suggested flat spots on it then diamond dust files work well. ~10mm wide flat spots are suggested to be added to the shaft ~40mm from the bottom end and on the top end to allow better grip for the clamping screws. The top end can then be inserted into the Barrel Mount Rotary Attachment and then evenly tightening the two M3x12mm screws  to grip the shaft in the centre of the mounting hole. Onto the yaw shaft the {12 Limit Switch Arm - Internal} and a 60 tooth, 5mm bore GT2 pulley also need to be installed, with the limit switch arm (approx 45mm from the end of the shaft) first then the pulley (approx 30mm from the end of the shaft). Both these items should be installed loosely as they will need adjustment later.  

The final step for assembly of the barrel mount is to attach the rotary bearing. This also attaches on the underside of the barrel mount. The holes in this bearing are not large enough so need to be drilled or filed out to fit M5 screws. This is screwed into place using low profile M5x8mm screws which mate into the tee nuts that were inserted earlier into the 1st and 5th extrusions. It is essential to get the rotary bearing centred on the base again so loosely tighten the bearing, then measure to make sure it is central, tighten up and then measure again to make sure it is still central. 

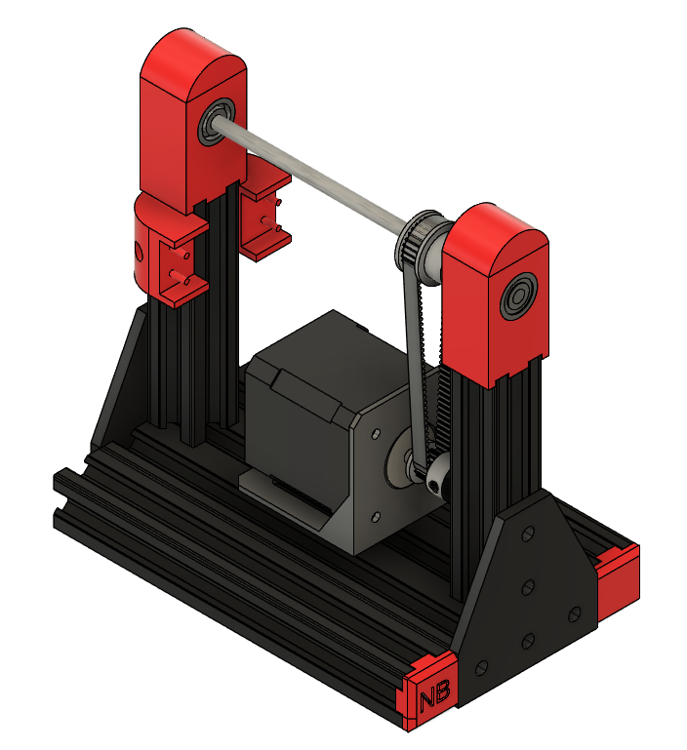
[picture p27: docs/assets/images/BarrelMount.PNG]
Barrel Mount Assembly


## Turret Base Assembly

The turret base is where all the mechanical parts come together to make an overall system. A number of 3D printed parts need to have other parts assembled into them first before they are incorporated so we will start with these. 

### Water and Power Inlet  
This 3D printed part {09 Water and Power Inlet} has a number of parts mounted in and behind it. This part can be found in the diagram below.

First up the extra plastic material need to support printing has to be removed from holes 1 and 4. The holes on the front are the smaller holes so work from the front to clear these holes out - there is only a 0.2mm layer of plastic so this should be straight forward. Also remove any support material that may be found down the parts that slide into the aluminum extrusions and slide this part in and out of an extrusion a few times to make sure of a good and easy fit before populating it with the other parts. 

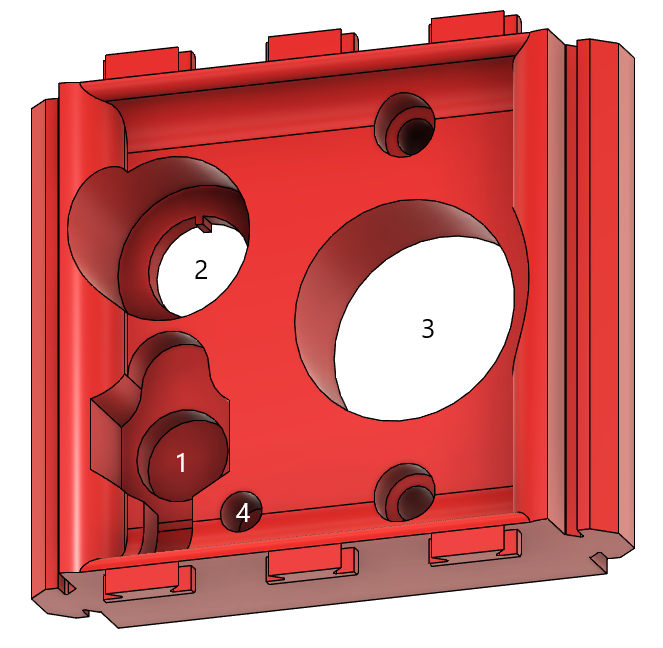
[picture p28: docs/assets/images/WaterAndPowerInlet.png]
Water and Power Inlet


After this the power inlet connector can be installed. The O-ring should be placed over the connector and then the connector can be inserted from the rear through hole (1), the protective cover can then be put over the connector thread (with the actual protective cover hanging down into the gap at the bottom (near hole (4)) and then the nut can be screwed down until tight. The metal washer in the pack is not used. 

The LED is installed next - it may be easier to wire the LED before installing to make the soldering easier - see the Electronics Assembly section for more information. This is simply pushed into hole (4) from the rear. A dab of glue can be used if required to secure it.

The main power switch is installed next. This installed from the rear though hole (2) with the nut/protective cover being installed from the front to hold the switch in place.The terminals of the switch need to be carefully bent upwards until they are flat with the bottom of the switch to avoid them fouling the battery when it is installed.

Lastly the solenoid valve assembly is inserted into hole (3) and is fixed in place using two M4x16mm screws through the smaller holes above and below the main inlet. Once mounted in place the G3/4 to hosepipe adaptor can be screwed onto the inlet thread. It may be easier to measure and mount the wires for the solenoids at this point - see the Electronics Assembly section for more information.

### Fan Inlet
The {00 Fan Inlet} only has a fan mounted in it but it can be tricky to get this mounted! A diagram of the part can be found below, it is shown upside down in this picture so that the fan can be easily seen. The outside part of this piece will be the visible side (with holes in it )

The fan is inserted from via the hole in the hole on the outside part. But before putting the fan in the cable for the fan must be fed through the hole for this purpose by the top right hand edge of the fan in the diagram (hole not visible). Once the cable has been pulled through to the other side then the fan can be dropped in and fixed in place using M4x20mm screws from the front with M4 hex nuts on the rear. The screws can be accessed via the holes in the front of the fan inlet and it is suggested to start with the lower nuts on the back (held in place with pliers) to make assembly easier. Once the fan is fixed in place then the four {01 Fan Inlet Hole Cover} parts can be pushed into place in the four holes on the front of the unit to aid in waterproofing. 

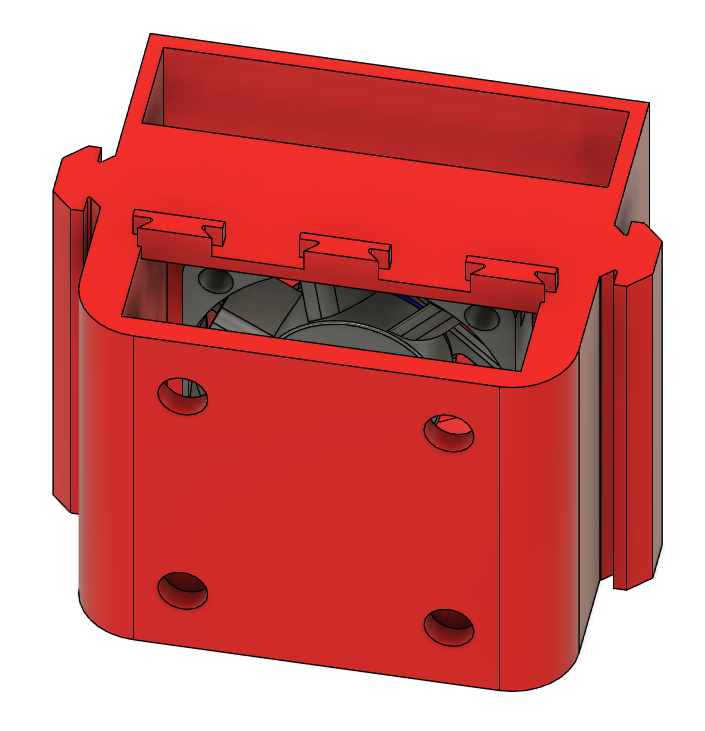
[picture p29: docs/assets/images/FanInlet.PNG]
Fan Inlet


### Rotary Bearing Mount
The {04 Rotary Bearing Mount} provides the interface point between the Turret Base and the Turret Barrel Mount. The four holes nearest the middle need to be cleaned out from the plastic used to support the printing - this can be easily done by pushing an M5 screw through each hole from the top. This part can now be attached to the rotary bearing (that was joined to the base of the Turret Barrel Mount in a previous step). M5x12mm hex head screws are used to do this via the inner 4 holes. The hex head screws are inserted from the underneath and then the rotary bearing is fixed in place with half height M5 hex nuts. The screw locations on the bottom of the Rotary Bearing Mount have a hex outline to allow for easy assembly. 

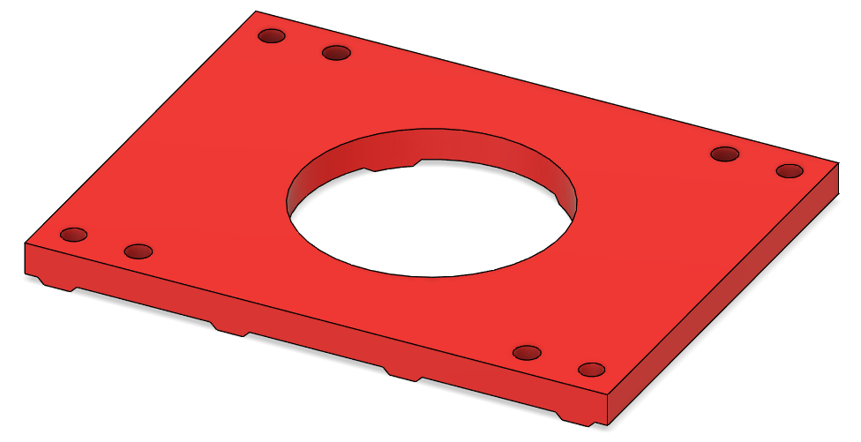
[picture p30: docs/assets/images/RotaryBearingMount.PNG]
Rotary Bearing Mount


### Turret Base Top Plate and Plumbing
This part holds all the tubing between the water control solenoids and the turret barrel. It is much easier to assemble the tubing into this top plate before assembling the top plate into the overall turret base. The photo below shows the final tubing assembly. First from the braided hose cut two 130mm lengths, two 65mm lengths and six 45mm lengths. This hose needs to be able handle mains pressure water and thinner more flexible hose will likely be pushed off the connectors (as I found out!). Two identical pairs of hoses need to be constructed. One pair is made from two 45mm lengths joined with a 90 degree tube elbow, with one of the 45mm lengths joined onto a 3D printed {07 Tubing Adaptor} and all the joints secured with hose clips (behind the barbs) as shown. The other pair is made from a 3D printed {07 Tubing Adaptor} joined onto a 130mm length with the other end joined to a 90 degree tube elbow which is also joined to a 65mm length which is in turn joined to a 45mm length with another 90 degree tube elbow, and all the joints secured with hose clips (behind the barbs) as shown.

Six 320mm lengths of corrugated hose are then required four of which are securely glued into the tube adaptors using a liberal amount of epoxy glue worked well into recess for the tube to push into and ensuring the tube goes past the small internal barb in the tube adaptor to help keep the tube in place. Note that this end of the tube adaptor has four thin plastic supports to help with printing these adaptors - these can be easily removed with side cutters before inserting the tubes in. Once the tubing has been left long enough to let the epoxy set firm the tubes can be inserted through the Turret Base Top Plate taking care to insert the tubes that are going to be used for water in the correct holes to line up with the barrel - in the design as built this is the outer four holes with the centre two reserved for dummy tubes.

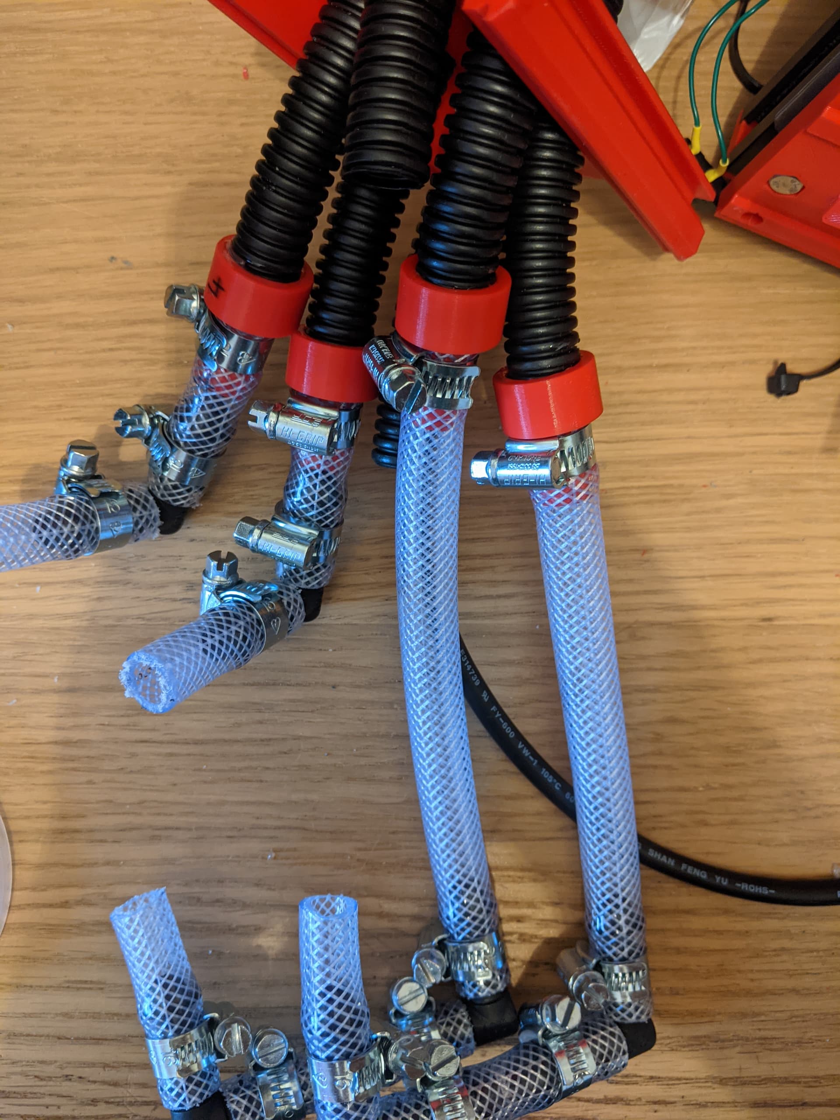
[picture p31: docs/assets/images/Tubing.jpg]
Tubing


### Turret Base 
The main part of the turret base is assembled from aluminum extrusions held together with 3D printed profile joiners and 2 hole joining plate brackets and double L shaped brackets. Other 3D printed parts slot into these aluminum extrusions to complete the turret base. The rear/side view of the Turret Base can be found below to aid with assembly.

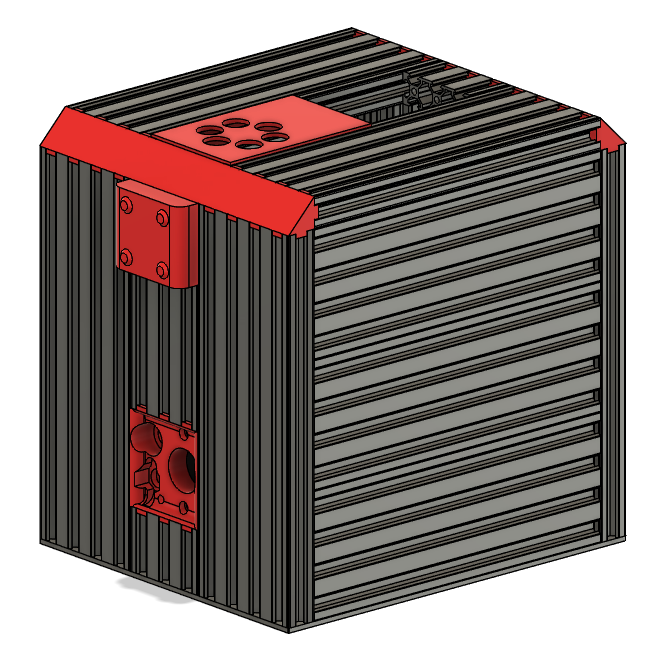
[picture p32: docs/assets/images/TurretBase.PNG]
Turret Base


First assemble the two sides; these are each simply made from three 20x80x220mm aluminum extrusions held together with four 3D printed profile joiners, one at each end of each join to make a stack of three aluminum extrusions. 

Now the rear can be assembled. This is assembled by taking one 20x80x240mm (tapped at the bottom end) extrusion and sliding the fan inlet onto one edge and aligning it with the top of the extrusion noting that the fan inlet hole covers show the outside of the unit. Underneath this fan inlet join a 20x60x90mm extrusion to the same side at the fan inlet using two 3D printed profile joiners and push up flush under the fan inlet, noting that the protrusions under the fan inlet will lock into the gaps in the top of this extrusion. Under this slide in the Water and Power Inlet and again push flush with the extrusion above, again engaging the protrusions in the extrusion. Lastly add a 20x60x40mm extrusion (tapped at the bottom end) using 2 more 3D printed profile joiners and push home. Now on the other side of the items that have just been installed another 20x80x240mm (tapped at the bottom end) extrusion can be slid on using 4 more 3D profile joiners to firmly attach this part. 

The top can now be assembled. This starts with a 20x80x220mm extrusion into which is slid the Turret Base Top Plate. This top plate is aligned against one end of this extrusion, on the other end of the extrusion is a 20x60x30mm extrusion held in place with a 3D printed profile joiner. The gap that is left between the two is where the Rotary Bearing Mount will go but this has to be assembled later to allow the yaw shaft to be inserted into the internal bearing mount. Now another 20x80x220mm extrusion is slide on the side of the Turret Base Top Plate and shorter extrusion, again joined with a 3D printed profile joiner. 

The sides and front can now be joined together using seven double universal L brackets, twenty six tee nuts and twenty six M5x8mm screws as shown in the photo below - note that this photo is taken with the turret base upside down and with the water and power inlet and top plate / tubes removed for ease of photography. Note the bracket on the lefthand side in this photo facing the other way - this is to support the back side of the battery when it is installed. 

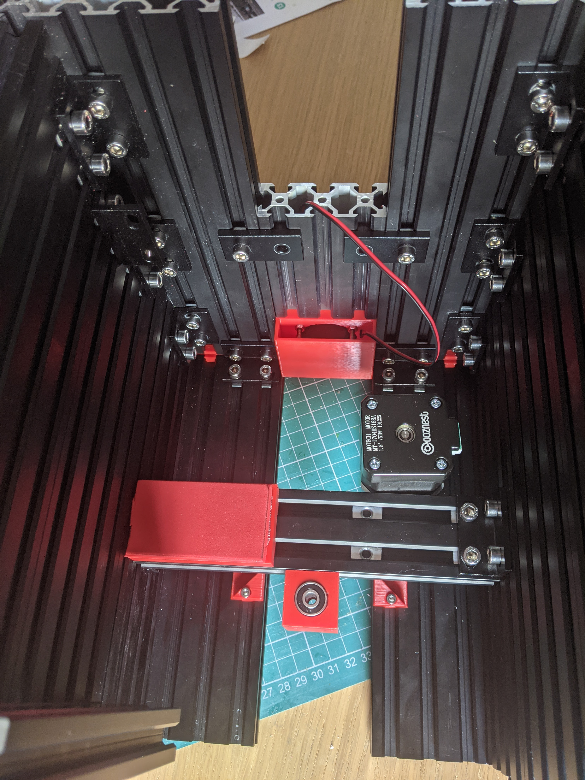
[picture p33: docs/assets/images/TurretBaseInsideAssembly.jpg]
Turret Base Inside Assembly


Once the sides and front have been joined then the top can be added and fixed in place two double universal L brackets, eight tee nuts and eight M5x8mm screws as shown in the photo below. Before fixing the top on the {05 Top Rear Edge} part must be put between the extrusions and slotted into place as shown in the diagram above. This part is impossible to add once the top has been screwed in place. 

Once these parts have been screwed together then the pipework can be attached to the solenoid valves outlet pipes, noting that hose clips need to be used on all these joins (behind the barbs on the solenoid value outputs as before). The long tubes with double 90 degree bends join to the bottom outlets and the shorter tubes join to the top outlets. It is quite a tight fit to get all this pipework in and the cable clips tightened up and a flexible shaft hex driver really helps to get the hose clips tightened up.

Next to install is the Internal Bearing and Motor Mount. To install this insert two tee nuts in the second extrusion slot down on the right hand side (looking from the front - see the diagram below) and two tee nuts in the fourth extrusion slot down on the left hand side and then insert the Internal Bearing and Motor Mount (motor first) and line the L brackets on the end of them with the cage nuts that have just been placed in the extrusions and loosely screw them in place so that the Internal Bearing and Motor Mount can be slid back and forth in the turret base, as an initial positioning it will go about a third of the way back.

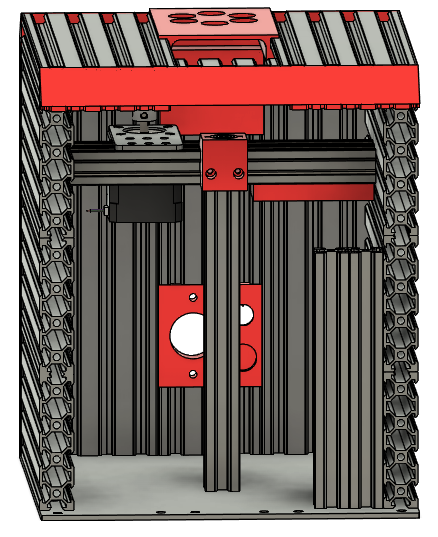
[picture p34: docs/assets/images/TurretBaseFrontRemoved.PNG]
Turret Base Front Removed


The Barrel Mount and Rotary Bearing Mount assembly can now be offered up to the hole in the top of the Turret Base. The 252mm GT2 timing belt must be put around at least the yaw shaft, and ideally positioned around the pulleys before it is located in the bearings. The Rotary Bearing Mount must be pushed flush with the Turret Base Top Plate. The yaw shaft needs to go through the centre of the bearings in the bearing mount and so the Barrel Mount and Rotary Bearing Mount assembly needs to be moved back and forwards until it is in a suitable location. Once in place then the Rotary Bearing Mount needs to be screwed down to the top of the Turret Base using four M5x12mm hex head screws and four tee nuts slid into the extrusion slots 3rd out from the edges of the top. These screws can be done up by rotating the turret barrel mount out of the way to allow access. After checking that the Rotary Bearing Mount is still flush with the Turret Base Top Plate these screws can be tightened down. Now the screws in the L brackets that join the Internal Bearing and Motor Mount to the sides of the Turret base can be tightened down progressively checking for continued free yaw rotation of the barrel mount as they are tightened. Once these are tightened then timing belt can be installed over the two pulleys, the pulleys can be adjusted to they are in a plane with each other and the yaw motor can be adjusted and tightened down so that the timing belt is tight between the two pulleys - it should be possible to push the timing belt in slightly in the middle but with minimal deflection. 

Next the yaw microswitches can be installed into the {02 Internal Limit Switch Holder - Left} and {03 Internal Limit Switch Holder - Right}. An M3 square nut can be installed in each of them and an M3x12mm screw inserted into each until just before it comes out the other side of the profile insert. The microswtich holders can then be inserted into the 4th slot in from each side on the Turret Base top. The locking screws should be nearest the front (where the microswitches have been slid in from) and the microswitch levers should point towards the back of the Turret Base. The Limit Switch Arm can now be adjusted to be the right height to activate the microswitches. With the turret barrel mount pointing directly forward the limit switch arm must point directly towards the back of the unit. The locking screw can now be tightened to hold it in place. 

The front battery support post (20x40x180mm tapped at the bottom end) can now be added using a double L shaped bracket to fix it to the bottom of the Internal Bearing and Motor Mount using the tee nuts that were placed in an earlier step and two M5x8mm screws. The side battery mount will be fixed in place later once the batter has been added.

The baseplate can now be added. 4 tee nuts need to be slid into the bottom edge extrusion slot on both sides and the baseplate is fixed in place using sixteen M5x8mm screws (6 for the rear, 4 for each side and 2 for the front battery support post).

Last to build is the front of the turret base ready for the installation of the Electronics Enclosure and Camera Housing. Take one 20x80x240mm (tapped at bottom end) extrusion and join one side to a 20x60x210mm (tapped at bottom end) extrusion using two 3D printed profile joiners, then add another one 20x80x240mm (tapped at bottom end) extrusion onto the other side of the 210mm extrusion using two more 3D printed profile joiners. Ensure that the tapped holes are all at the bottom and that the 30mm gap for the Camera Housing is at the top. Some 2 hole brackets can be used with tee nuts and M5x8mm screws if required to add some rigidity to the front panel. The front panel will be populated and installed as part of the electronics assembly.  
 
### Turret Barrel Installation
The last of the mechanical assembly is to install the Turret Barrel. A 150mm length of 5mm hardened steel rod is required as the pitch shaft, which can be cut and worked as before. A flat side should be made along the whole length of this shaft leaving 22mm each end untouched to allow for locking on the various components on the shaft in place. Starting from the right hand side (looking from the front) and with the flat side on the shaft facing directly downwards pass the shaft through the two bearings in the housing then put a 202mm GT2 timing belt between the pulley on the motor and a 40 tooth, 5mm bore GT2 pulley positioned so that the locking grub screws are towards the middle away from the bearing housing then insert the pitch shaft into this pulley (note this will be tight fit as there is no other adjustment for this belt). Next add the Barrel itself and push the pitch shaft through it, then add {10 Limit Switch Arm - Barrel} with the flat edge facing away from the barrel. Lastly push the pitch shaft through the other two bearings to complete the installation of the barrel. With the shaft in place the components can all be adjusted to their final positions. Starting with the barrel - this needs to be placed in the middle of the two uprights - exact isn’t essential but will help with more accurate tracking and firing - then the two locking screws can be tightened up. The pulley can then be adjusted so that it is in a plane with the pulley on the motor and its grub screws can be tightened and lastly the limit switch arm can be adjusted and locked in place with its locking screw. The limit switch arm should be in the middle of the two limit switches when the barrel is pointing roughly parallel. Epoxy can be added to help ensure it stays in the correct position. 

[{Home}](README.md) [{Next}](ElectronicsAssembly.md)

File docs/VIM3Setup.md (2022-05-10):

# VIM3 Setup
Before the VIM3 is installed in the system it has to be configured with an operating system image and basic setup to allow connection to it once it is installed into the Water Auto Turret because there is no access to the USB-C or Ethernet ports once installed. The serial debug port is brought out onto the top of the main board for any issues that need a hard wired connection. 

First the latest version of Ubuntu Server needs to be installed into the EMMC following the instructions [here](https://docs.khadas.com/linux/vim3/InstallOsIntoEmmc.html). Then do a full system upgrade as per the instructions [here](https://docs.khadas.com/linux/vim3/UpgradeSystem.html). 

Next the WiFi connection has to be setup following the instructions [here](https://docs.khadas.com/linux/vim3/Wifi.html#server). Alternatively it may be useful to set the VIM3 up as a hotspot following the instructions [here](https://docs.khadas.com/linux/vim3/WifiApstaMode.html) to avoid the need for a wifi network but I haven't tested this yet and have just used a wifi hotspot from my phone to connect the Water Auto Turret to when out of range of my home WiFi. 

Finally make sure that it is possible to SSH into the VIM3 over the WiFi connection and then one can either shutdown the VIM3 ready for installation into the Electronics Enclosure or install the rest of the software as described below.

## Software Installation 
The following steps have to be carried out to install the software for the Water Auto Turret:
* WiringPi-Python is required for GPIO access this is installed by following the instructions [here](https://github.com/khadas/WiringPi-Python#manual-build) for Python 3.
* Clone the GitHub repository for the Water Auto Turret
  * `git clone https://github.com/neilbirtles/WaterAutoTurret`
* Change to the project directory, create a Python virtual environment with access to the system site packages to pick up WiringPi-Python and activate it
  * `cd WaterAutoTurret`
  * `python3 -m venv venv --system-site-packages`
  * `source venv/bin/activate`
* Install PIP
  * `sudo apt install python3-pip`
* Install all dependencies:
  * `pip3 install matplotlib`
  * `pip3 install install numpy`
  * `wget https://github.com/khadas/ksnn/blob/master/ksnn/ksnn-1.3-py3-none-any.whl`
  * `pip3 install ksnn-1.3-py3-none-any.whl`
  * `pip3 install Flask`
  * `pip3 install Bootstrap-Flask`
  * `pip3 install spidev`

Once everything is installed then the web app can be run using the following command:
* `python3 autoturret.py`

The web interface should then be available on the VIM3’s IP address on port 5000, but some errors may be thrown if the other hardware is not available (i.e. this is benign just run on the bare VIM3).

[{Home}](README.md) [{Next}](SoftwareDescription.md)

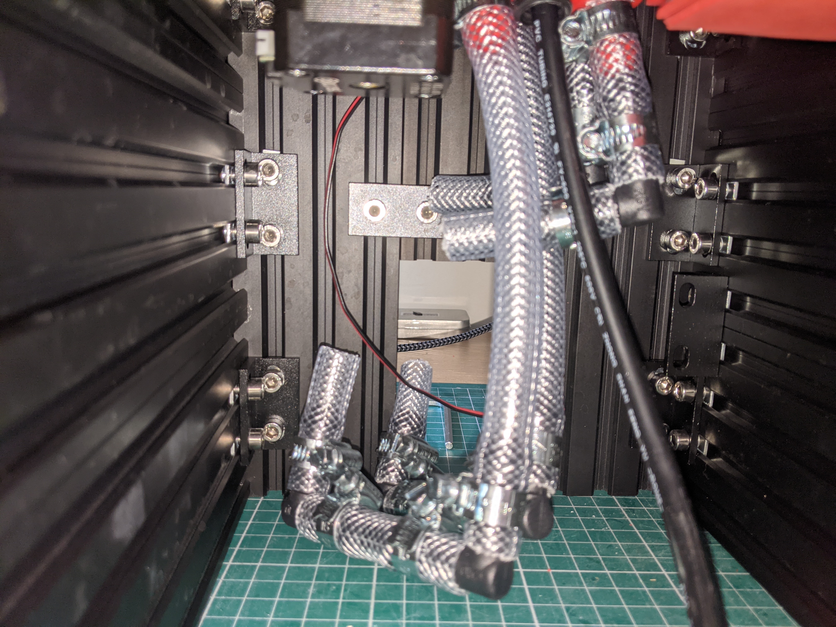
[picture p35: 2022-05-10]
docs/assets/images/InstalledTubing.jpg

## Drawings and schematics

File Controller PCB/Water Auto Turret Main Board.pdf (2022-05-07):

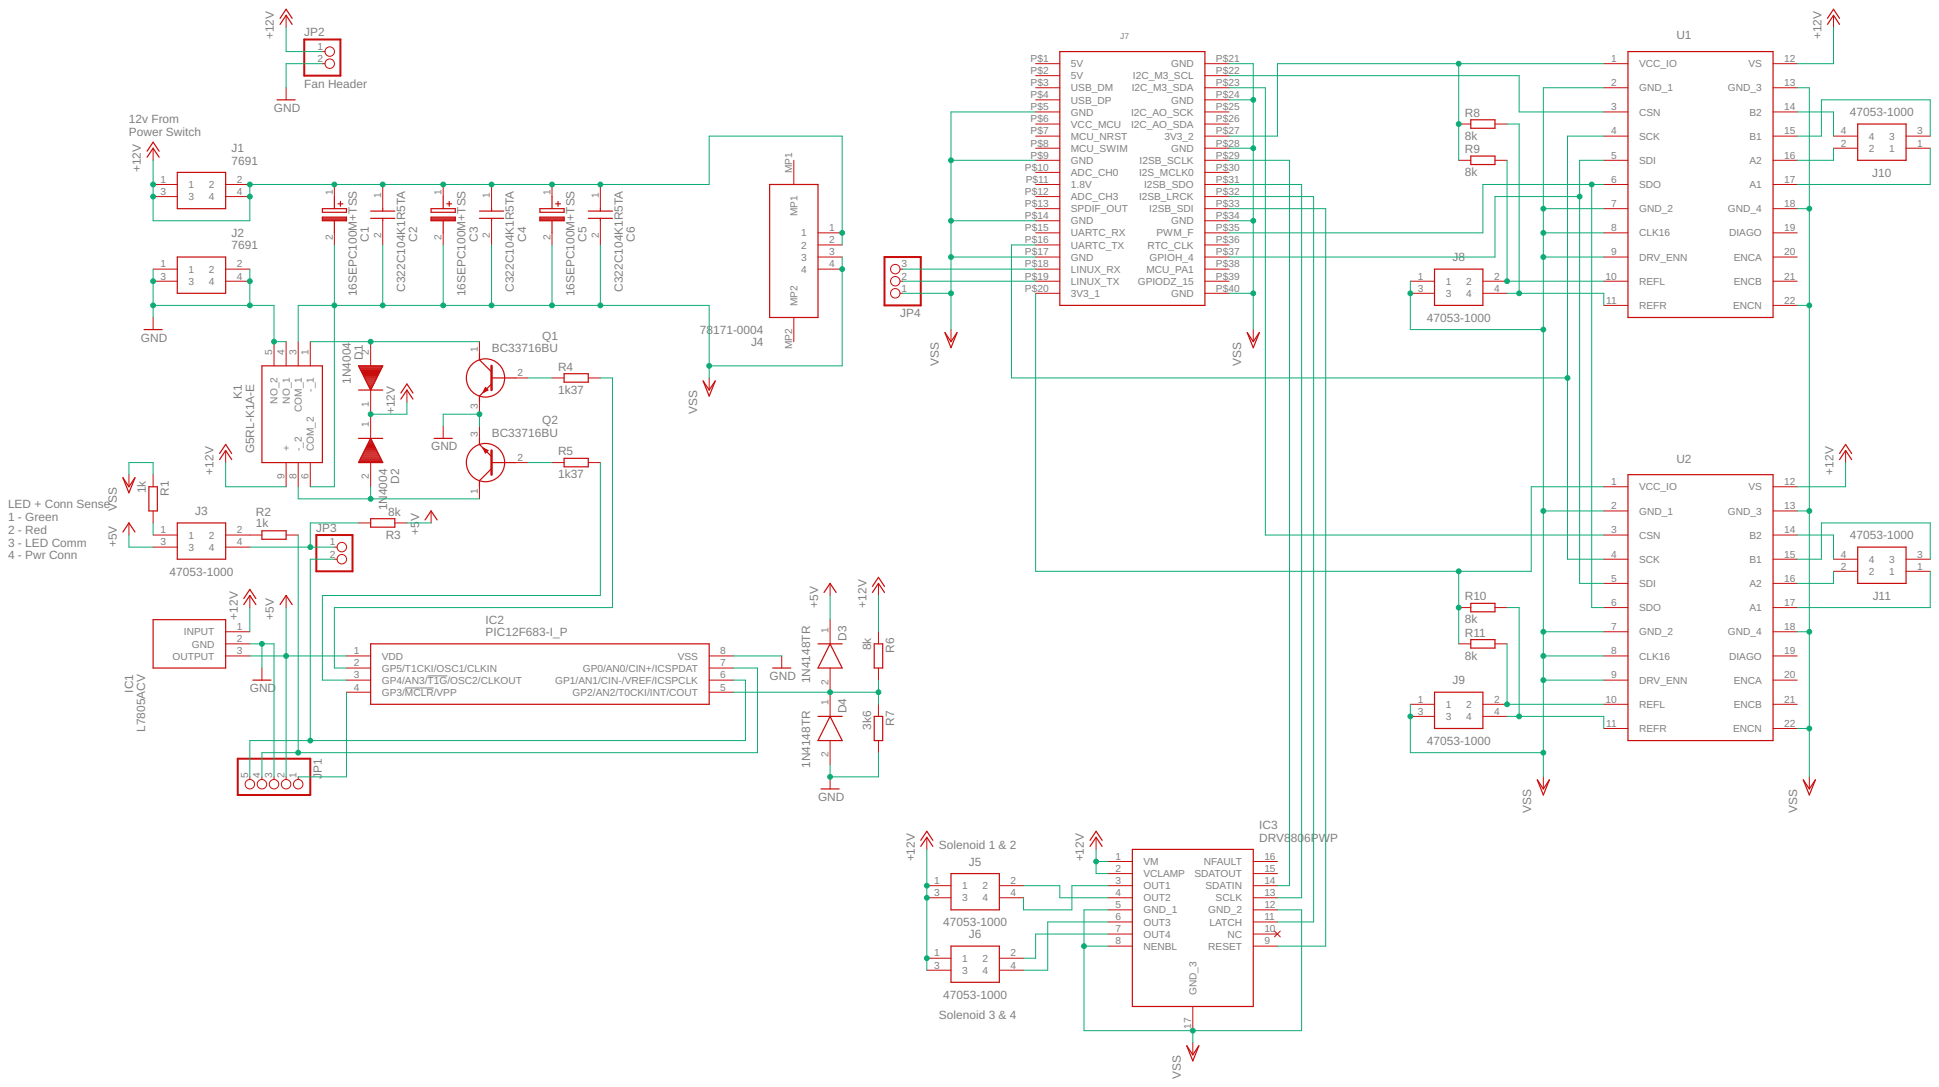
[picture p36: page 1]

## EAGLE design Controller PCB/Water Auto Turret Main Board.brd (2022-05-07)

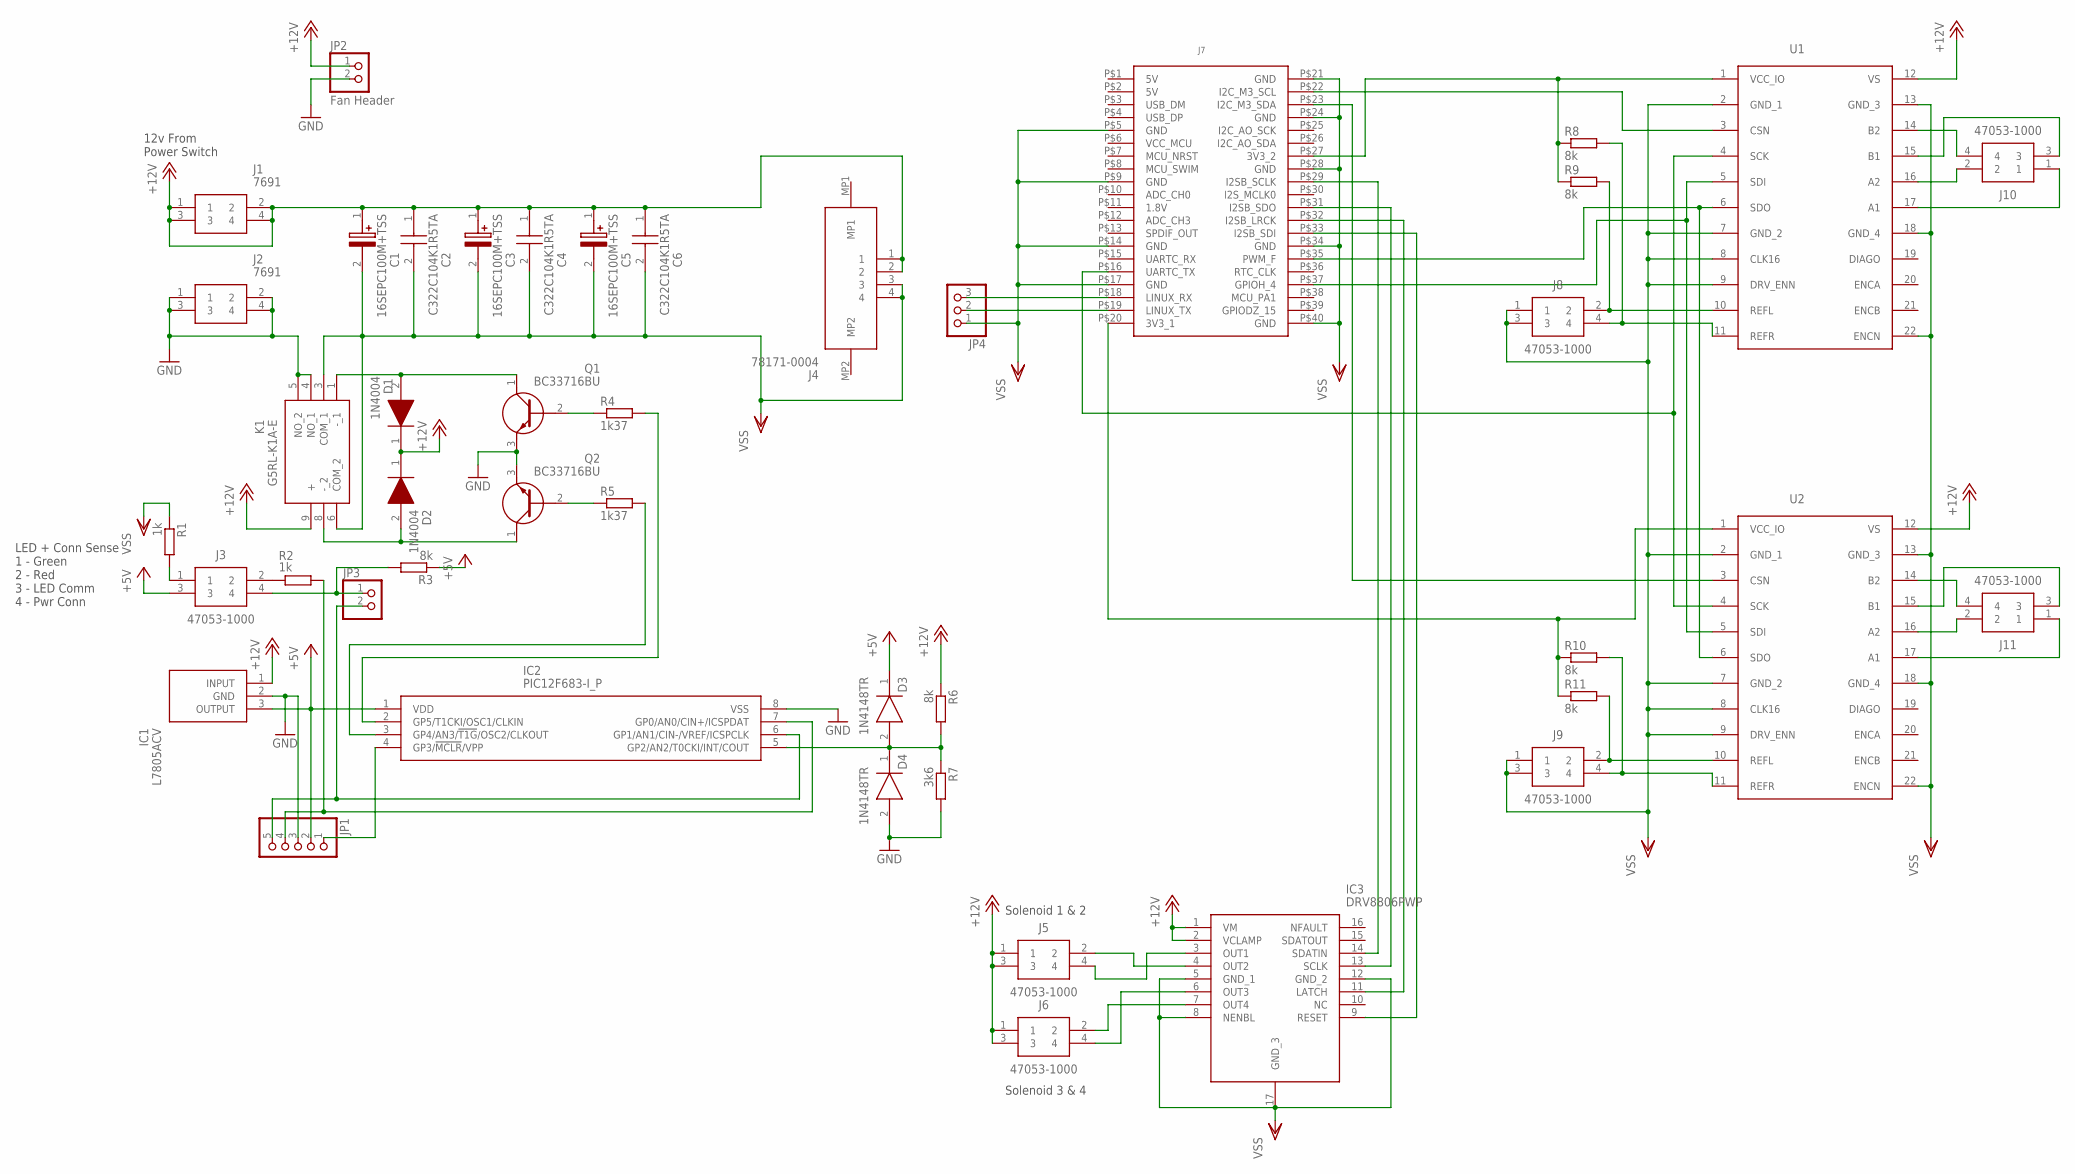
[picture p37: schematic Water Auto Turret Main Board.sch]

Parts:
C1, C3, C5: 16SEPC100M+TSS; CAPPRD250W45D630H600
C2, C4, C6: C322C104K1R5TA
D1, D2: 1N4004; DIOAD1408W86L464D236
D3, D4: 1N4148TR; DIOAD990W55L340D162
IC1: L7805ACV; TO255P460X1020X2008-3P
IC2: PIC12F683-I_P; DIP781W56P254L950H533Q8N
IC3: DRV8806PWP; SOP65P640X120-17N
J1, J2: 7691
J3, J6, J8, J9, J10, J11: 47053-1000
J4: 78171-0004; 781710004
J5: 47053-1000; MANUFACTURER_PART_NUMBER Solenoid 1 & 2
J7: VIM3GPIO
JP1: PINHD-1X5; 1X05
JP2: Fan Header; 1X02
JP3: PINHD-1X2; 1X02
JP4: PINHD-1X3; 1X03
K1: G5RL-K1A-E; G5RLK1AE
Q1, Q2: BC33716BU; TO-92
R1, R2: 1k; V234/12
R3: 8k; 0309V
R4, R5: 1k37; V234/12
R6, R8, R9, R10, R11: 8k; V234/12
R7: 3k6; 0309V
U1, U2: TMC5160-BOB

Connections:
5V: J7.P$1 (5V), J7.P$2 (5V)
+5V: D3.1 (K), IC1.3 (OUTPUT), IC2.1 (VDD), J3.3, JP1.2, R3.1
+12V: C1.1 (+), C2.1, C3.1 (+), C4.1, C5.1 (+), C6.1, D1.1 (K), D2.1 (K), IC1.1 (INPUT), IC3.1 (VM), IC3.2 (VCLAMP), J1.1, J1.2, J1.3, J1.4, J4.1, J4.2, J5.1, J5.3, J6.1, J6.3, JP2.1, K1.9 (+), R6.1, U1.12 (VS), U2.12 (VS)
GND: D4.2 (A), IC1.2 (GND), IC2.8 (VSS), J2.1, J2.2, J2.3, J2.4, JP1.3, JP2.2, K1.4 (NO_1), K1.5 (NO_2), Q1.3 (E), Q2.3 (E), R7.2
unnamed: IC3.4 (OUT2), J5.2
unnamed: IC3.3 (OUT1), J5.4
unnamed: IC3.6 (OUT3), J6.4
unnamed: IC3.7 (OUT4), J6.2
unnamed: J3.1, R1.2
unnamed: D1.2 (A), K1.1 (-_1), Q1.1 (C)
unnamed: D2.2 (A), K1.8 (-_2), Q2.1 (C)
unnamed: J3.2, R2.1
unnamed: IC2.4 (GP3/!MCLR!/VPP), JP1.1
unnamed: Q1.2 (B), R4.1
unnamed: IC2.7 (GP0/AN0/CIN+/ICSPDAT), JP1.4, R2.2
unnamed: IC2.6 (GP1/AN1/CIN-/VREF/ICSPCLK), JP1.5, JP3.2
unnamed: Q2.2 (B), R5.1
unnamed: IC2.3 (GP4/AN3/!T1G!/OSC2/CLKOUT), R5.2
unnamed: IC2.2 (GP5/T1CKI/OSC1/CLKIN), R4.2
unnamed: D3.2 (A), D4.1 (K), IC2.5 (GP2/AN2/T0CKI/INT/COUT), R6.2, R7.1
unnamed: J3.4, JP3.1, R3.2
unnamed: J7.P$35 (PWM_F), U1.6 (SDO), U2.6 (SDO)
unnamed: J7.P$37 (GPIOH_4), U1.5 (SDI), U2.5 (SDI)
unnamed: J7.P$16 (UARTC_TX), U1.4 (SCK), U2.4 (SCK)
unnamed: J10.4, U1.14 (B2)
unnamed: J10.3, U1.15 (B1)
unnamed: J10.1, U1.17 (A1)
unnamed: J10.2, U1.16 (A2)
unnamed: J11.4, U2.14 (B2)
unnamed: J11.2, U2.16 (A2)
unnamed: J11.1, U2.17 (A1)
unnamed: J11.3, U2.15 (B1)
unnamed: J8.2, R9.2, U1.10 (REFL)
unnamed: J8.4, R8.2, U1.11 (REFR)
unnamed: J9.2, R11.2, U2.10 (REFL)
unnamed: J9.4, R10.2, U2.11 (REFR)
unnamed: J7.P$20 (3V3_1), R10.1, R11.1, U2.1 (VCC_IO)
unnamed: IC3.14 (SDATIN), J7.P$29 (I2SB_SCLK)
unnamed: IC3.13 (SCLK), J7.P$31 (I2SB_SDO)
unnamed: IC3.11 (LATCH), J7.P$32 (I2SB_LRCK)
unnamed: IC3.9 (RESET), J7.P$33 (I2SB_SDI)
unnamed: J7.P$18 (LINUX_RX), JP4.3
unnamed: J7.P$19 (LINUX_TX), JP4.2
unnamed: J7.P$27 (3V3_2), R8.1, R9.1, U1.1 (VCC_IO)
unnamed: J7.P$22 (I2C_M3_SCL), U1.3 (CSN)
unnamed: J7.P$23 (I2C_M3_SDA), U2.3 (CSN)
VSS: C1.2 (-), C2.2, C3.2 (-), C4.2, C5.2 (-), C6.2, IC3.5 (GND_1), IC3.8 (NENBL), IC3.12 (GND_2), IC3.17 (GND_3), J4.3, J4.4, J7.P$5 (GND), J7.P$9 (GND), J7.P$14 (GND), J7.P$17 (GND), J7.P$21 (GND), J7.P$24 (GND), J7.P$28 (GND), J7.P$34 (GND), J7.P$40 (GND), J8.1, J8.3, J9.1, J9.3, JP4.1, K1.3 (COM_1), K1.6 (COM_2), R1.1, U1.2 (GND_1), U1.7 (GND_2), U1.8 (CLK16), U1.9 (DRV_ENN), U1.13 (GND_3), U1.18 (GND_4), U1.22 (ENCN), U2.2 (GND_1), U2.7 (GND_2), U2.8 (CLK16), U2.9 (DRV_ENN), U2.13 (GND_3), U2.18 (GND_4), U2.22 (ENCN)

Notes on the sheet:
Solenoid 1 & 2
Solenoid 3 & 4
12v From Power Switch
LED + Conn Sense 1 - Green 2 - Red 3 - LED Comm 4 - Pwr Conn

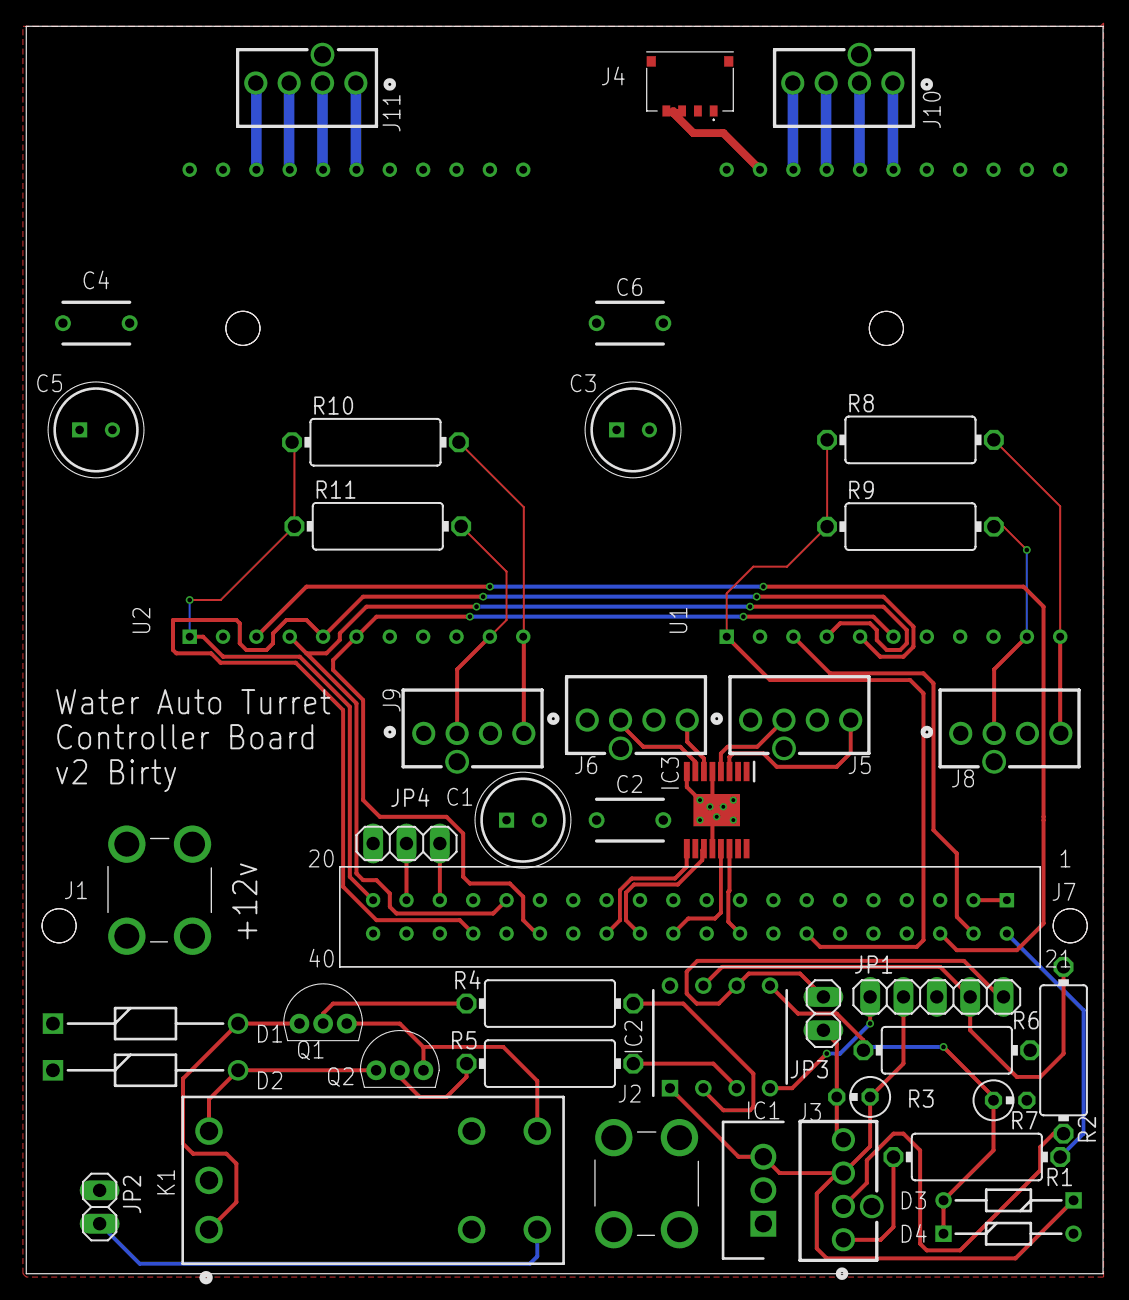
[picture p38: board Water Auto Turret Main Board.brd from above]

Board: 2 copper layers, 82.0 x 95.0 mm, 44 parts (0 on the bottom side), 47 nets.

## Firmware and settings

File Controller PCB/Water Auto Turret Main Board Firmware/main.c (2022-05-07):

/*
 * File:   main.c
 * Author: neilb
 * 
 */

// CONFIG
#pragma config FOSC = INTOSCIO  // Oscillator Selection bits (INTOSCIO oscillator: I/O function on RA4/OSC2/CLKOUT pin, I/O function on RA5/OSC1/CLKIN)
#pragma config WDTE = OFF        // Watchdog Timer Enable bit (WDT enabled)
#pragma config PWRTE = OFF      // Power-up Timer Enable bit (PWRT disabled)
#pragma config MCLRE = OFF       // MCLR Pin Function Select bit (MCLR pin function is MCLR)
#pragma config CP = OFF         // Code Protection bit (Program memory code protection is disabled)
#pragma config CPD = OFF        // Data Code Protection bit (Data memory code protection is disabled)
#pragma config BOREN = ON       // Brown Out Detect (BOR enabled)
#pragma config IESO = ON        // Internal External Switchover bit (Internal External Switchover mode is enabled)
#pragma config FCMEN = ON       // Fail-Safe Clock Monitor Enabled bit (Fail-Safe Clock Monitor is enabled

#include "main.h"
#include <xc.h>



//the following line needs to be added to a target program to allow the bootloader
//to detect that 
//const unsigned char app_loaded __at(0xFFF) = 0x55;

void SYSTEM_Initialize(void)
{
    PIN_MANAGER_Initialize();
    OSCILLATOR_Initialize();
    WDT_Initialize();
}

void PIN_MANAGER_Initialize(void)
{
    //CIN pins are configured as I/O, COUT pin is configured as I/O, Comparator output disabled, Comparator off
    CMCON0 = 0x07;
    //GP2, GP1 inputs, all others outputs
    TRISIO = 0x06;
    //GP2 analog input, AD conversion FOSC/64
    ANSEL = 0x64;
    //weak pull up enabled
    OPTION_REGbits.nGPPU = 0;
    //WPU1 enabled, all others disabled
    WPU = 0x02;
}

void OSCILLATOR_Initialize(void)
{
    // SCS FOSC; IRCF 500KHz; 
    OSCCON = 0x30;
    // TUN 0; 
    OSCTUNE = 0x00;
    // SBOREN disabled; 
    PCONbits.SBODEN = 0x00;
}

void WDT_Initialize(void)
{
    // WDTPS 1:65536; SWDTEN OFF; 
    WDTCON = 0x16;
}

void main(void) {
    
    int batt_voltage_ok = 1;
    int batt_charging = 0; 
    
    SYSTEM_Initialize();
    
    //Flash red LED on startup, leave on as power to VIM3 board is off at this point
    Red_LED = 0;
    __delay_ms(250);
    Red_LED = 1;
    __delay_ms(250);
    Red_LED = 0;

    //make sure that the turn on main power is off
    Turn_On_Main_Power = 0;
    //turn the main power off on startup
    Turn_Off_Main_Power = 1;
    __delay_ms(250);
    Turn_Off_Main_Power = 0;
    //let settle for 1 second
    __delay_ms(1000);
    
    //get the inverse of initial value to trigger at least one loop of power setup
    batt_charging = !Batt_Charge_Indicator;
    
    Turn_On_Main_Power = 1;
    __delay_ms(250);
    Turn_On_Main_Power = 0;
    //turn off the red LED
    Red_LED = 1;
    
    //check for battery charging and low battery voltage - if either detected
    // then turn off the power to the rest of the board and the VIM3
    while (1) {
        //measure battery voltage TODO
            //if ok then red LED off, set flag to allow power on
            //if not ok then red LED on and turn off power to main board, set flag to prevent power on
        
        //see if battery charging state has changed since last time
        if (Batt_Charge_Indicator != batt_charging){
            //debounce and check if still different
            __delay_ms(100);
            if (Batt_Charge_Indicator != batt_charging){
                //status has changed so save new status
                batt_charging = Batt_Charge_Indicator;
                //A Batt_Charge_Indicator value of 0 indicates that no charging 
                //plug is joined in.
                //If battery is not charging and lower power flag not set then 
                //turn on power to main board
                if (!batt_charging && batt_voltage_ok){
                    //latching relay so power coil, wait for it to settle, then remove power
                    Turn_On_Main_Power = 1;
                    __delay_ms(250);
                    Turn_On_Main_Power = 0;
                    //turn off the red LED
                    Red_LED = 1;
                //otherwise the battery is charging or in a low voltage state
                // so turn off power to main board
                }else{
                    //latching relay so power coil, wait for it to settle, then remove power
                    Turn_Off_Main_Power = 1;
                    __delay_ms(250);
                    Turn_Off_Main_Power = 0;
                    //turn on the red LED
                    Red_LED = 0;
                }
            }
        }
        
        //only check every half second
        __delay_ms(500);
    }
}

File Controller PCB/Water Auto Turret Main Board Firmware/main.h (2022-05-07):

/* Microchip Technology Inc. and its subsidiaries.  You may use this software 
 * and any derivatives exclusively with Microchip products. 
 * 
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
 * IN NO EVENT WILL MICROCHIP BE LIABLE FOR ANY INDIRECT, SPECIAL, PUNITIVE, 
 * INCIDENTAL OR CONSEQUENTIAL LOSS, DAMAGE, COST OR EXPENSE OF ANY KIND 
 * WHATSOEVER RELATED TO THE SOFTWARE, HOWEVER CAUSED, EVEN IF MICROCHIP HAS 
 * BEEN ADVISED OF THE POSSIBILITY OR THE DAMAGES ARE FORESEEABLE.  TO THE 
 * FULLEST EXTENT ALLOWED BY LAW, MICROCHIP'S TOTAL LIABILITY ON ALL CLAIMS 
 * IN ANY WAY RELATED TO THIS SOFTWARE WILL NOT EXCEED THE AMOUNT OF FEES, IF 
 * ANY, THAT YOU HAVE PAID DIRECTLY TO MICROCHIP FOR THIS SOFTWARE.
 *
 * MICROCHIP PROVIDES THIS SOFTWARE CONDITIONALLY UPON YOUR ACCEPTANCE OF THESE 
 * TERMS. 
 */

/* 
 * File:   
 * Author: 
 * Comments: 
 * Revision history: 
 */

// This is a guard condition so that contents of this file are not included
// more than once.  
#ifndef XC_HEADER_TEMPLATE_H
#define	XC_HEADER_TEMPLATE_H

#include <xc.h> // include processor files - each processor file is guarded.  

#define _XTAL_FREQ 500000

#define Red_LED                 GPIObits.GP0
#define Batt_Charge_Indicator   GPIObits.GP1
#define Batt_voltage_Measure    GPIObits.GP2
#define Turn_On_Main_Power      GPIObits.GP4
#define Turn_Off_Main_Power     GPIObits.GP5

void SYSTEM_Initialize(void);
void OSCILLATOR_Initialize(void);
void WDT_Initialize(void);
void PIN_MANAGER_Initialize (void);

#endif	/* XC_HEADER_TEMPLATE_H */

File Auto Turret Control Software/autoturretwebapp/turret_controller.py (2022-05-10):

from ctypes import *
import time
import numpy as np
from ksnn.api import KSNN
from ksnn.types import *

import cv2 as cv

DEBUG = False

GRID0 = 13
GRID1 = 26
GRID2 = 52
LISTSIZE = 85
SPAN = 3
OBJ_THRESH = 0.5
NMS_THRESH = 0.6
FRAME_WIDTH = 1920
FRAME_HEIGHT = 1080

CLASSES = ("person", "bicycle", "car","motorbike ","aeroplane ","bus ","train","truck ","boat","traffic light",
           "fire hydrant","stop sign ","parking meter","bench","bird","cat","dog ","horse ","sheep","cow","elephant",
           "bear","zebra ","giraffe","backpack","umbrella","handbag","tie","suitcase","frisbee","skis","snowboard","sports ball","kite",
           "baseball bat","baseball glove","skateboard","surfboard","tennis racket","bottle","wine glass","cup","fork","knife ",
           "spoon","bowl","banana","apple","sandwich","orange","broccoli","carrot","hot dog","pizza ","donut","cake","chair","sofa",
           "pottedplant","bed","diningtable","toilet ","tvmonitor","laptop	","mouse	","remote ","keyboard ","cell phone","microwave ",
           "oven ","toaster","sink","refrigerator ","book","clock","vase","scissors ","teddy bear ","hair drier", "toothbrush ")

def sigmoid(x):
	return 1 / (1 + np.exp(-x))


def process(input, mask, anchors):

	anchors = [anchors[i] for i in mask]
	grid_h, grid_w = map(int, input.shape[0:2])

	box_confidence = sigmoid(input[..., 4])
	box_confidence = np.expand_dims(box_confidence, axis=-1)

	box_class_probs = sigmoid(input[..., 5:])

	box_xy = sigmoid(input[..., :2])
	box_wh = np.exp(input[..., 2:4])
	box_wh = box_wh * anchors

	col = np.tile(np.arange(0, grid_w), grid_w).reshape(-1, grid_w)
	row = np.tile(np.arange(0, grid_h).reshape(-1, 1), grid_h)

	col = col.reshape(grid_h, grid_w, 1, 1).repeat(3, axis=-2)
	row = row.reshape(grid_h, grid_w, 1, 1).repeat(3, axis=-2)
	grid = np.concatenate((col, row), axis=-1)

	box_xy += grid
	box_xy /= (grid_w, grid_h)
	box_wh /= (416, 416)
	box_xy -= (box_wh / 2.)
	box = np.concatenate((box_xy, box_wh), axis=-1)

	return box, box_confidence, box_class_probs

def filter_boxes(boxes, box_confidences, box_class_probs):
	box_scores = box_confidences * box_class_probs
	box_classes = np.argmax(box_scores, axis=-1)
	box_class_scores = np.max(box_scores, axis=-1)
	pos = np.where(box_class_scores >= OBJ_THRESH)

	boxes = boxes[pos]
	classes = box_classes[pos]
	scores = box_class_scores[pos]

	return boxes, classes, scores

def nms_boxes(boxes, scores):
	x = boxes[:, 0]
	y = boxes[:, 1]
	w = boxes[:, 2]
	h = boxes[:, 3]

	areas = w * h
	order = scores.argsort()[::-1]

	keep = []
	while order.size > 0:
		i = order[0]
		keep.append(i)

		xx1 = np.maximum(x[i], x[order[1:]])
		yy1 = np.maximum(y[i], y[order[1:]])
		xx2 = np.minimum(x[i] + w[i], x[order[1:]] + w[order[1:]])
		yy2 = np.minimum(y[i] + h[i], y[order[1:]] + h[order[1:]])

		w1 = np.maximum(0.0, xx2 - xx1 + 0.00001)
		h1 = np.maximum(0.0, yy2 - yy1 + 0.00001)
		inter = w1 * h1

		ovr = inter / (areas[i] + areas[order[1:]] - inter)
		inds = np.where(ovr <= NMS_THRESH)[0]
		order = order[inds + 1]
	keep = np.array(keep)
	return keep

def yolov3_post_process(input_data):
	masks = [[6, 7, 8], [3, 4, 5], [0, 1, 2]]
	anchors = [[10, 13], [16, 30], [33, 23], [30, 61], [62, 45],
			[59, 119], [116, 90], [156, 198], [373, 326]]

	boxes, classes, scores = [], [], []
	for input,mask in zip(input_data, masks):
		b, c, s = process(input, mask, anchors)
		b, c, s = filter_boxes(b, c, s)
		boxes.append(b)
		classes.append(c)
		scores.append(s)

	boxes = np.concatenate(boxes)
	classes = np.concatenate(classes)
	scores = np.concatenate(scores)

	nboxes, nclasses, nscores = [], [], []
	for c in set(classes):
		inds = np.where(classes == c)
		b = boxes[inds]
		c = classes[inds]
		s = scores[inds]

		keep = nms_boxes(b, s)

		nboxes.append(b[keep])
		nclasses.append(c[keep])
		nscores.append(s[keep])

	if not nclasses and not nscores:
		return None, None, None

	boxes = np.concatenate(nboxes)
	classes = np.concatenate(nclasses)
	scores = np.concatenate(nscores)

	return boxes, classes, scores

def draw(image, boxes, scores, classes):
	for box, score, cl in zip(boxes, scores, classes):
		x, y, w, h = box
		x *= image.shape[1]
		y *= image.shape[0]
		w *= image.shape[1]
		h *= image.shape[0]
		if DEBUG: print(f"[turret contoller] Detection Class: {CLASSES[cl]} and Score: {score:.0%}")
		if DEBUG: print(f"[turret contoller] Detection box (left,top,right,down): [{(x):.1f}, {(y):.1f}, {(x+w):.1f}, {(y+h):.1f}]")
		top = max(0, np.floor(x + 0.5).astype(int))
		left = max(0, np.floor(y + 0.5).astype(int))
		right = min(image.shape[1], np.floor(x + w + 0.5).astype(int))
		bottom = min(image.shape[0], np.floor(y + h + 0.5).astype(int))
		
		cv.rectangle(image, (top, left), (right, bottom), (0, 255, 0), 2)
		cv.putText(image, f"{CLASSES[cl]} {score:.0%}", (top, left - 6), cv.FONT_HERSHEY_SIMPLEX, 0.6, (0, 0, 255), 2)

def target_turret(image):
	cv.drawMarker(image, (int(image.shape[1]/2),int(image.shape[0]/2)), color=(0,0,255), markerType=cv.MARKER_STAR)
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

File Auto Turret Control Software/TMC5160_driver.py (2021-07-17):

from time import sleep

#Debug printing flag
DEBUG = False

# SPI CONSTANTS
OUTPUT = 1
OUTPUT_LOW = 0
OUTPUT_HIGH = 1

#TMC5160 Registers - pulled from TMC5160 datasheet - https://www.trinamic.com/fileadmin/assets/Products/ICs_Documents/TMC5160A_Datasheet_Rev1.15.pdf 
#General Configuration Registers
GCONF       = 0x00
GSTAT       = 0x01
IFCNT       = 0x02
SLAVECONF   = 0x03
INP_OUT     = 0x04
X_COMPARE   = 0x05
OTP_PROG    = 0x06
OTP_READ    = 0x07
FACT_CONF   = 0x08
SHORT_CONF  = 0x09
DRV_CONF    = 0x0A
GSCALE      = 0x0B
OFFSET_READ = 0x0C
#Velocity Dependent Driver Feature Control Register Set
IHOLD_IRUN  = 0x10
TPOWERDOWN  = 0x11
TSTEP       = 0x12
TPWMTHRS    = 0x13
TCOOLTHRS   = 0x14
THIGH       = 0x15
#Ramp Generator Motion Control Register Set
RAMPMODE    = 0x20
XACTUAL     = 0x21
VACTUAL     = 0x22
VSTART      = 0x23
A1          = 0x24
V1          = 0x25
AMAX        = 0x26
VMAX        = 0x27
DMAX        = 0x28
D1          = 0x2A
VSTOP       = 0x2B
TZEROWAIT   = 0x2C
XTARGET     = 0x2D
#Ramp Generator Driver Feature Control Register Set
VDCMIN      = 0x33
SWMODE      = 0x34
RAMPSTAT    = 0x35
XLATCH      = 0x36
#Encoder Registers
ENCMODE     = 0x38
X_ENC        = 0x39
ENC_CONST   = 0x3A
ENC_STATUS  = 0x3B
ENC_LATCH   = 0x3C
ENC_DEVI    = 0x3D
#Motor Driver Registers
MSLUT0      = 0x60
MSLUT1      = 0x61
MSLUT2      = 0x62
MSLUT3      = 0x63
MSLUT4      = 0x64
MSLUT5      = 0x65
MSLUT6      = 0x66
MSLUT7      = 0x67
MSLUTSEL    = 0x68
MSLUTSTART  = 0x69
MSCNT       = 0x6A
MSCURACT    = 0x6B
CHOPCONF    = 0x6C
COOLCONF    = 0x6D
DCCTRL      = 0x6E
DRV_STATUS  = 0x6F
PWMCONF     = 0x70
PWM_SCALE   = 0x71
PWM_AUTO    = 0x72
LOST_STEPS  = 0x73

class TMC5160_driver:

    def __init__(self, SPI_interface, GPIO, chip_select_pin, sense_res_max_i):
        #The SPI interface to use for communicating with the device - must be compatible with SPIDEV
        self.__interface = SPI_interface
        #The chip select pin this driver will use to select the right chip
        self.__chip_select_pin = chip_select_pin
        self.__GPIO = GPIO
        #Make sure teh CS pin is set as an output
        self.__GPIO.pinMode(self.__chip_select_pin, OUTPUT)
        #Set the CS line high to disable comms with the chip
        self.__GPIO.digitalWrite(self.__chip_select_pin, OUTPUT_HIGH)
        #The sense resistor defines the max current - used in other calcs - e.g. global scaler
        self.__sense_res_max_i = sense_res_max_i

        #The TMC5160 sends status back with every transmission, stored here
        self.__latest_SPI_status = 0 #TMC5160_SPI_Status()
        #Flag used to store the success or not of the last write
        self.__last_write_success = True
        
        #Shadow registers for write only TMC5160 registers
        self.__global_scaler = 0
        self.__ihold = 0
        self.__irun = 0
        self.__ihold_delay = 0
        self.__short_conf = 0 # needs to be set to power on defaults
        #default ramp values to give a slow movement 
        self.__VSTART = 1
        self.__A1 = 100
        self.__V1 = 250 
        self.__AMAX = 25
        self.__VMAX = 1000
        self.__DMAX = 70
        self.__D1 = 100
        self.__VSTOP = 100
        
        #tracks the homing status
        self.__homed = False
        self.__max_left_steps = 0
        self.__max_right_steps = 0
    
    def __read_from_TMC5160(self, address):
        #transfers are always 40bits, MSB first
        #39-32 address bits, 31-0 data bits
        #bit 39 indicates direction - 0 for read and 1 for write - for read AND with 0x7F
        #read from the device by sending dummy data, then the requested data is returned 
        # on the next device read, so read twice as not using sequential register reads
        read_data = [address & 0x7F, 0, 0, 0, 0]
        read_buffer = self.__send_data(read_data)
        read_buffer = self.__send_data(read_data)
        
        #first byte is status info, so save it
        self.__latest_SPI_status = read_buffer[0]

        #return the 32bit word response
        return self.__extract_data_from_response(read_buffer)
    
    def __write_to_TMC5160(self, address, data):
        #transfers are always 40bits, MSB first
        #39-32 address bits, 31-0 data bits
        #bit 39 indicates direction - 0 for read and 1 for write - for write OR with 0x80
        #setup a write buffer as need to send in bytes, and put the modified addres in byte 0
        write_buffer = [address | 0x80, 0, 0, 0, 0]
        #split and move the data into the right byte positions
        #byte 0 still AND with 0xFF to remove any extra data above bit 31
        write_buffer[1] = 0xFF & (data >> 24)
        write_buffer[2] = 0xFF & (data >> 16)
        write_buffer[3] = 0xFF & (data >> 8)
        write_buffer[4] = 0xFF & data
        
        if DEBUG:
            print("Address: " +hex(address))
            print("Address OR'ed: " + hex(address | 0x80))
            print("Data: " + hex(data))
            print("Write Buffer pre send: ", end='')# + str(write_buffer))
            print('[{}]'.format(', '.join(hex(x) for x in write_buffer)))

        #write the data to the chip
        self.__send_data(write_buffer)
        #sleep(0.01)
        #perform a read (any reg works) to get the previously written info back. Using GCONF
        sent_dat = self.__send_data([0, 0, 0, 0, 0])
        check_data = self.__twos_compliment(self.__extract_data_from_response(sent_dat))

        if DEBUG:
            print("Rx Sent Data: ", end='')# + str(sent_dat))
            print('[{}]'.format(', '.join(hex(x) for x in sent_dat)))
            print("Check Data: " + hex(check_data))
        
        if check_data == data:
            #if there is match to the sent data then
            self.__last_write_success = True
        else:
            #if there is a mismatch then
            self.__last_write_success = False
            print("bad write")
            if DEBUG:
                print("bad write")
                print("data: " +hex(data))
                print("check data: " + hex(check_data))
                print("----------------------")
        
        #sleep(0.01)
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

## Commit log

2021-06-19 Published Controller Board
    [Water Auto Turret Main Board.brd, Water Auto Turret Main Board.sch]
2021-07-17 Solenoid and motor controller software and tests
2021-07-18 Moved files around to suit addition of web front end and added some initial info
    [appconfig.cfg]
2021-07-24 threading update
2021-07-27 Yolo i/f and turret move threads completed
    [appconfig.cfg]
2021-08-02 increase yaw motor current due to full mechanical load from pipework
2021-08-09 working tracking and water control
    [appconfig.cfg]
2022-05-03 Added 3D Printable Parts
    [00 Base.stl, 00 Bearing Mount.stl, 00 Electronics Enclosure Base (Supports Needed).stl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]
2022-05-03 Added missing 3D printed profile joiner parts
    [10 Profile Joiner.stl, 11 Profile Joiner - Horiz to Vert.stl]
2022-05-07 Rev2 PCB
    Fixes issues found on Rev1 PCB
    [Water Auto Turret Main Board.brd, Water Auto Turret Main Board.sch]
2022-05-07 Firmware for controller board
2022-05-10 switch from index.md to README.md
2022-05-10 fixed formatting and added back / next buttons
2022-05-10 Added 3D Model Export
    [2020_Simple_v7.f3d, 2020_Simple_v7.step, 2060 Profile Gap Sketch_v5.f3d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]
2022-05-15 Added BoM
    [BoMandEBS.xlsx]
